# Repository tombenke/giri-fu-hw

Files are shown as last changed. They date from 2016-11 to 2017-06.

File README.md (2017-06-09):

giri-fu-hw v2.0
===============

Hardware module of the giri-fu functional unit, that is a simple relay board, with its own MCU.

It is a proof of concept for a tiny autonomous device, that is able to control 24 VAC magnetic valves in real circumstances:

- wet and dirty environment,
- wide range of temperature,
- mechanical stress.

The [functional block diagram of the unit](docs/images/giri-fu-hw_fbd.png) below demonstrates how to connect it into its environment:

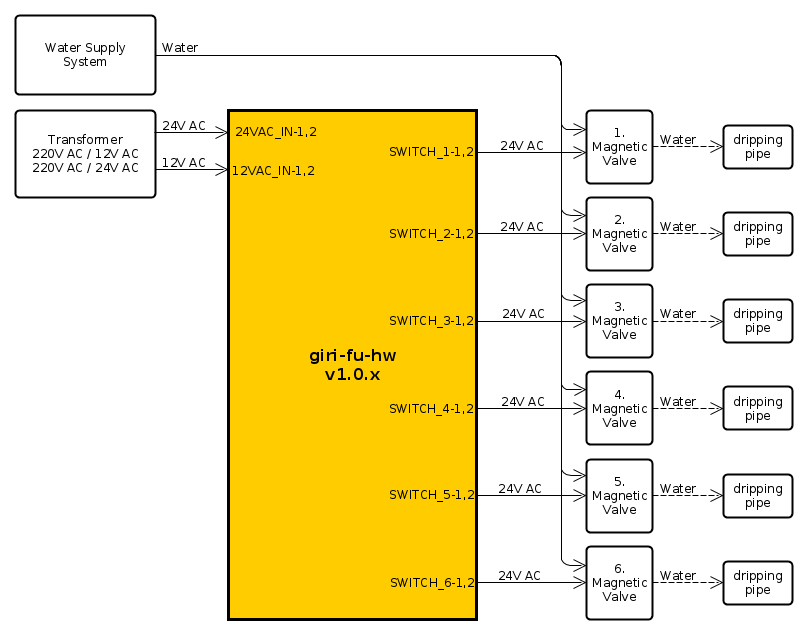
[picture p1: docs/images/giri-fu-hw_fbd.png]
functional block diagram of the unit


The v1.0.x version is just documenting [the early prototype](docs/images/prototype.jpg?raw=true "giri-fu-hw prototype"),
that was made on a raster panel. (Note: The PCB design differs from the raster panel version).

The PCB layout was intentionally designed to be very simple, in order to make it easy to reproduce with DIY technologies.

The top layer can be substituted with, straight jumper wires, so it is enought to make a one-sided panel, with the bottom layout.

The firmware implementation can be found in the [giri-fu firmware repository](https://github.com/tombenke/giri-fu).

## Features

- Standalone MCU (ATMega328P, 16MHz)
- High-voltage, high-current darlington transistor array (ULN2003A)
- 6 relays to switch 24V AC current, for magnetic valves (RSY-5)
- 12V AC input for Power supply
- RS-485 serial communication port

Dimensions: 3.6 x 2.15 x 0.5 inch

Boxing: The minimum required internal size of box: 4.75 x 3 x 1.5 inch

Mounting: N.A.

Inputs:

- 12V AC, min: ? A (TBD.)
- 24V AC, min: ? A (TBD.)

Outputs (6x):

- Carry current: 2 A
- Max. operating voltage: 125 VAC, 60 VDC
- Max. operating current: 1 A
- Max. switching capacity: 62.50 VA, 30W
- Min. permissible load: 1 mA, 5 VDC

## Artifacts

The `src` folder holds the EAGLE files:

- `src/giri-fu-hw.sch`
- `src/giri-fu-hw.brd`

The `dist` folder contains the final products for manufacturing:

- [The schematic diagram](dist/giri-fu-hw_sch.pdf)
- [The PCB layout](dist/giri-fu-hw_brd.pdf)
- [PCB top layer (to print)](dist/giri-fu-hw_top.pdf)
- [PCB bottom layer (to print)](dist/giri-fu-hw_bottom.pdf)

## References

- [giri-fu firmware](https://github.com/tombenke/giri-fu)
- [ATMega328P datasheet](http://www.atmel.com/Images/Atmel-42735-8-bit-AVR-Microcontroller-ATmega328-328P_datasheet.pdf)
- [Rayex RSY-5 relay datasheet](docs/datasheets/RSY-5G5V1K5V1_EN.pdf)
- [ULN2003A datsheet](https://www.sparkfun.com/datasheets/IC/ULN2003A.pdf)
- [Making of PCBs at home, DIY using inexpenive materials](https://www.youtube.com/watch?v=mv7Y0A9YeUc)
- [Heatless (cold) Toner Transfer (for PCB)](https://www.youtube.com/watch?v=HBIxvwZ_0og)
- [yEd - GraphML Editor, used for Functional Block Diagram creation](http://www.yworks.com/products/yed)
- [EAGLE PCB Design tool](https://cadsoft.io/)

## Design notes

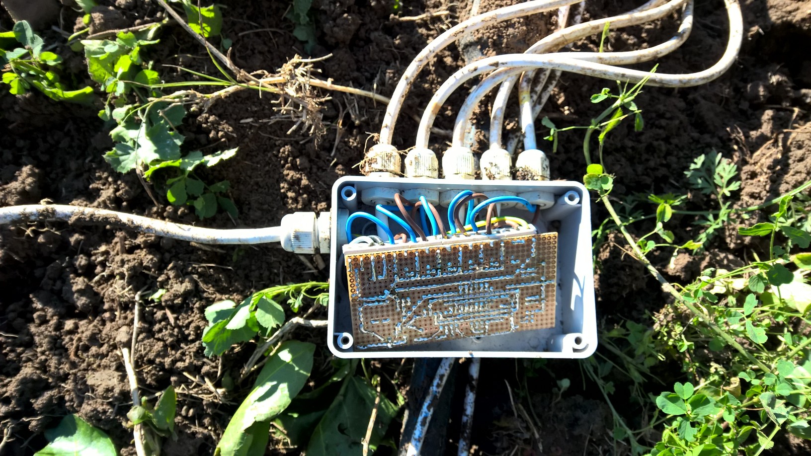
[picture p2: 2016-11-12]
docs/images/prototype.jpg

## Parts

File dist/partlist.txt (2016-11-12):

Partlist

Exported from giri-fu-hw.brd at 2016.11.12. 7:37

EAGLE Version 6.5.0 Copyright (c) 1988-2013 CadSoft

Assembly variant: 

Part     Value          Package      Library      Position (inch)       Orientation

C1       22p            C025-025X050 rcl          (1.75 1.65)           R0
C2       22p            C025-025X050 rcl          (1.5 1.65)            R0
C3       100n           C025-025X050 rcl          (1.85 1.4)            R270
C4       10uF           E2-5         adafruit     (2 1.4)               R270
C5                      E35-12       rcl          (0.95 1.35)           R180
D1       1N4004         DO41-10      diode        (0.7 0.5)             R0
D2       1N4004         DO41-10      diode        (0.5 0.65)            R0
D3       1N4004         DO41-10      diode        (0.5 0.95)            R180
D4       1N4004         DO41-10      diode        (0.7 0.8)             R180
IC1      ATMEGA168-20P  DIL28-3      adafruit     (2.65 1.85)           R180
IC2      7805T          TO220H       linear       (0.75 1.85)           R90
IC3      ULN2003AN      DIL16        uln-udn      (2.95 1.35)           R180
ISP1     AVRISP-6       AVRISP       adafruit     (2.4 1.35)            R0
K1       G5V1           G5V1         relay        (3.2 0.65)            R90
K2       G5V1           G5V1         relay        (2.8 0.65)            R90
K3       G5V1           G5V1         relay        (2.4 0.65)            R90
K4       G5V1           G5V1         relay        (2 0.65)              R90
K5       G5V1           G5V1         relay        (1.6 0.65)            R90
K6       G5V1           G5V1         relay        (1.2 0.65)            R90
Q1       16MHz          HC49U-V      adafruit     (1.6 1.85)            R180
R1       10K            0207/10      rcl          (2.15 1.4)            R270
R2       1M             0207/10      rcl          (1.6 2)               R180
X10                     W237-132     con-wago-508 (3.2 0.2)             R180
X11                     W237-132     con-wago-508 (2.8 0.2)             R180
X12                     W237-132     con-wago-508 (2.4 0.2)             R180
X13                     W237-132     con-wago-508 (2 0.2)               R180
X14                     W237-132     con-wago-508 (1.6 0.2)             R180
X15                     W237-132     con-wago-508 (1.2 0.2)             R180
X16                     W237-132     con-wago-508 (0.8 0.2)             R180
X17                     W237-132     con-wago-508 (0.4 0.2)             R180

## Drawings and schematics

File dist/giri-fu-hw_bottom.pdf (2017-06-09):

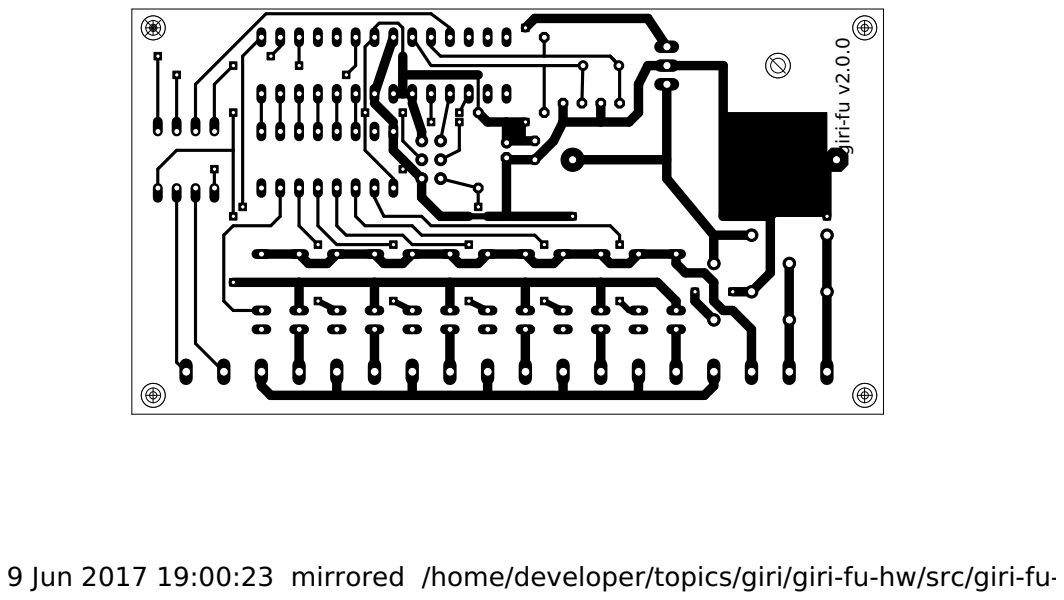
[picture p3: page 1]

9 Jun 2017 19:00:23 mirrored /home/developer/topics/giri/giri-fu-hw/src/giri-fu-hw.brd

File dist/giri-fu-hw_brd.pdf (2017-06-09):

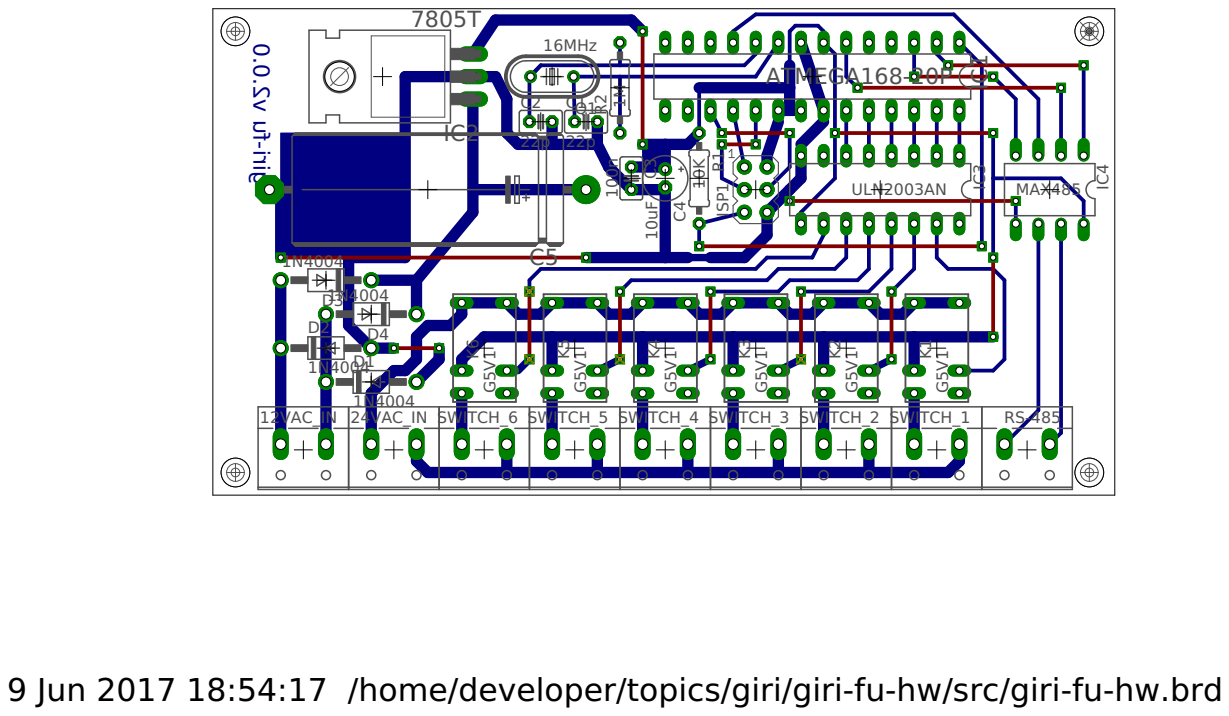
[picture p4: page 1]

9 Jun 2017 18:54:17 /home/developer/topics/giri/giri-fu-hw/src/giri-fu-hw.brd

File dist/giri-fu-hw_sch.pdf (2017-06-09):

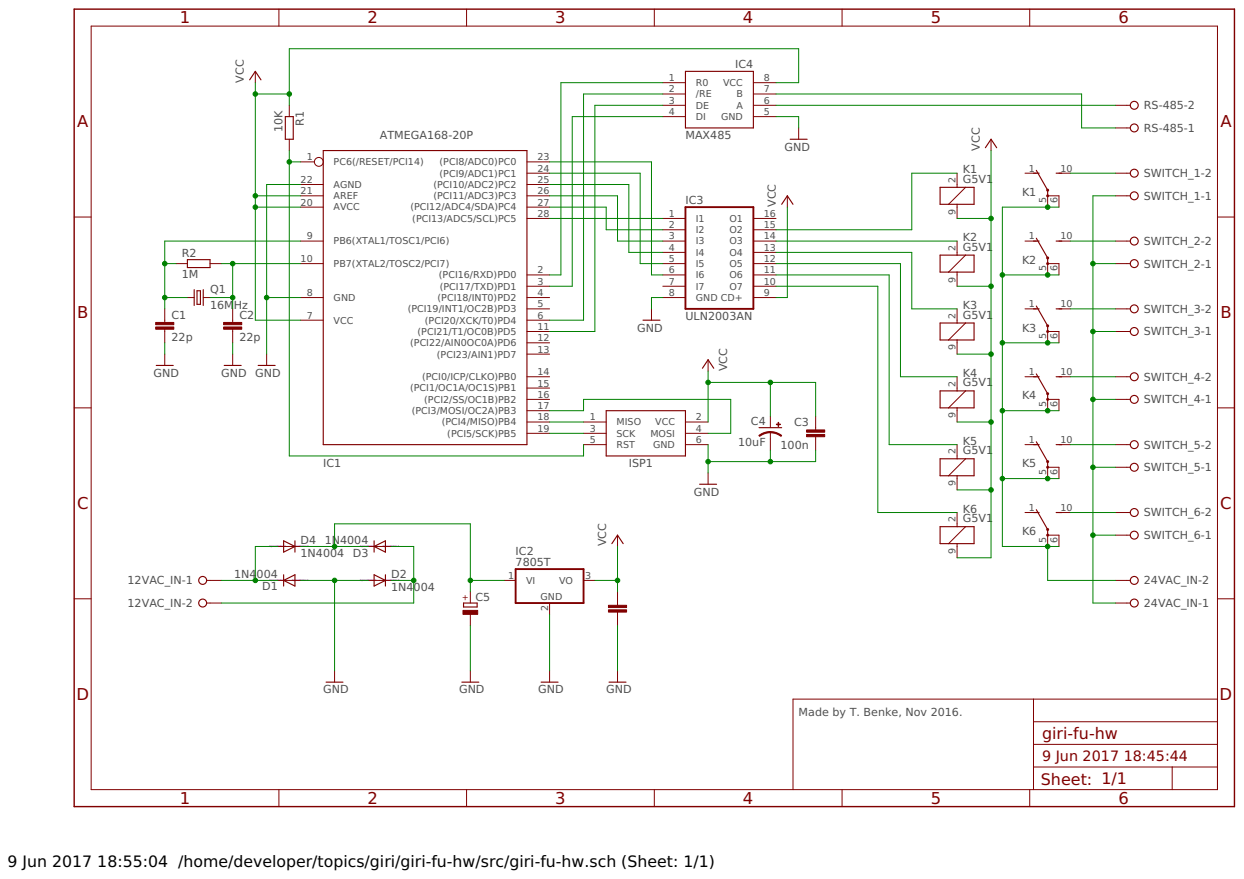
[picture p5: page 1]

24
25
26

5 | | 12
6 | | 11 O7

Made by T. Benke, Nov 2016.

Sheet: 1/1

9 Jun 2017 18:55:04 /home/developer/topics/giri/giri-fu-hw/src/giri-fu-hw.sch (Sheet: 1/1)

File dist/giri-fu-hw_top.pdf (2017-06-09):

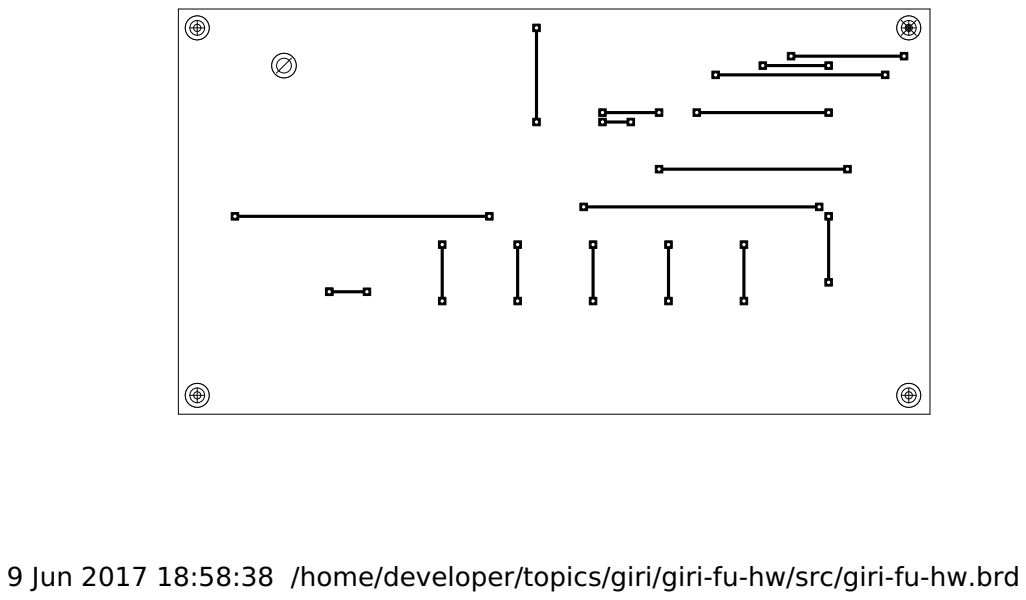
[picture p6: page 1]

9 Jun 2017 18:58:38 /home/developer/topics/giri/giri-fu-hw/src/giri-fu-hw.brd

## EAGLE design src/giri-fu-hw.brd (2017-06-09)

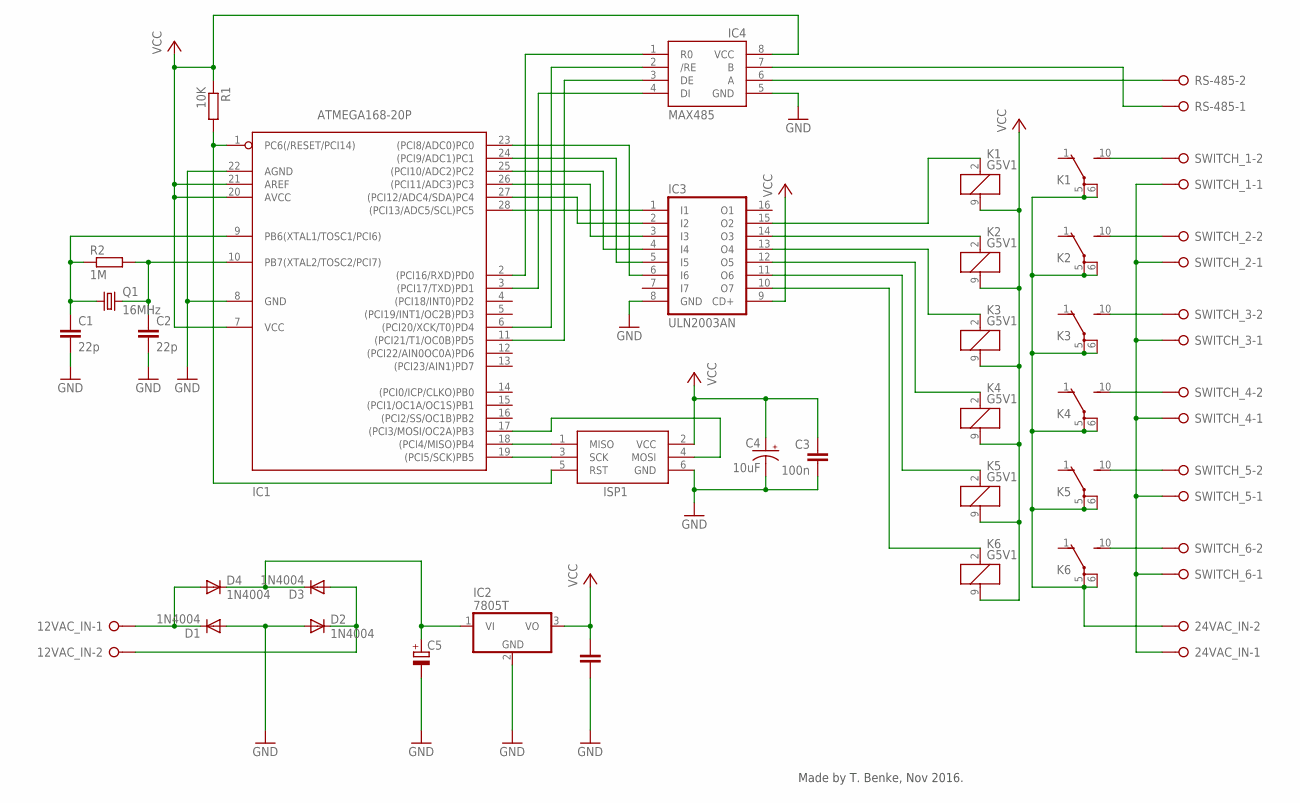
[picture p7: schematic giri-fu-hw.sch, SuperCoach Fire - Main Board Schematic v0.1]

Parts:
12VAC_IN, 24VAC_IN: W237-02P; W237-132
C1, C2: 22p; C025-025X050
C3: 100n; C025-025X050
C4: 10uF; E2-5
C5: CPOL-EUE35-12AXIAL; E35-12
D1, D2, D3, D4: 1N4004; DO41-10
IC1: ATMEGA168-20P; DIL28-3
IC2: 7805T; TO220H
IC3: ULN2003AN; DIL16
IC4: MAX485; DIL08
ISP1: AVRISP-6; AVRISP
K1, K2, K3, K4, K5, K6: G5V1
Q1: 16MHz; HC49U-V
R1: 10K; 0207/10
R2: 1M; 0207/10
RS-485: W237-02P; W237-132
SWITCH_1, SWITCH_2, SWITCH_3, SWITCH_4, SWITCH_5, SWITCH_6: W237-02P; W237-132

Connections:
GND: C1.2, C2.2, C3.2, C4.-, C5.-, D1.A, D2.A, IC1.8 (GND), IC1.22 (AGND), IC2.2 (GND), IC3.8 (GND), IC4.5 (GND), ISP1.6 (GND)
unnamed: IC1.23 ((PCI8/ADC0)PC0), IC3.6 (I6)
unnamed: IC1.24 ((PCI9/ADC1)PC1), IC3.5 (I5)
unnamed: 24VAC_IN.2, K1.5, K1.6, K2.5, K2.6, K3.5, K3.6, K4.5, K4.6, K5.5, K5.6, K6.5, K6.6
unnamed: IC1.25 ((PCI10/ADC2)PC2), IC3.4 (I4)
unnamed: IC1.28 ((PCI13/ADC5/SCL)PC5), IC3.1 (I1)
unnamed: IC1.26 ((PCI11/ADC3)PC3), IC3.3 (I3)
unnamed: IC1.27 ((PCI12/ADC4/SDA)PC4), IC3.2 (I2)
unnamed: C3.1, C4.+, IC1.7 (VCC), IC1.20 (AVCC), IC1.21 (AREF), IC2.3 (VO), IC3.9 (CD+), IC4.8 (VCC), ISP1.2 (VCC), K1.9 (2), K2.9 (2), K3.9 (2), K4.9 (2), K5.9 (2), K6.9 (2), R1.1
unnamed: IC3.10 (O7), K6.2 (1)
unnamed: IC3.11 (O6), K5.2 (1)
unnamed: IC1.19 ((PCI5/SCK)PB5), ISP1.3 (SCK)
unnamed: IC1.17 ((PCI3/MOSI/OC2A)PB3), ISP1.4 (MOSI)
unnamed: IC1.1 (PC6(/RESET/PCI14)), ISP1.5 (RST), R1.2
unnamed: C1.1, IC1.9 (PB6(XTAL1/TOSC1/PCI6)), Q1.1, R2.1
unnamed: C2.1, IC1.10 (PB7(XTAL2/TOSC2/PCI7)), Q1.2, R2.2
unnamed: IC1.18 ((PCI4/MISO)PB4), ISP1.1 (MISO)
unnamed: IC3.12 (O5), K4.2 (1)
unnamed: IC3.13 (O4), K3.2 (1)
unnamed: IC3.14 (O3), K2.2 (1)
unnamed: IC3.15 (O2), K1.2 (1)
unnamed: C5.+, D3.C, D4.C, IC2.1 (VI)
unnamed: 12VAC_IN.1, D1.C, D4.A
unnamed: 12VAC_IN.2, D2.C, D3.A
unnamed: IC4.6 (A), RS-485.2
unnamed: IC4.7 (B), RS-485.1
unnamed: IC1.2 ((PCI16/RXD)PD0), IC4.1 (R0)
unnamed: IC1.3 ((PCI17/TXD)PD1), IC4.4 (DI)
unnamed: K1.10 (S), SWITCH_1.2
unnamed: K2.10 (S), SWITCH_2.2
unnamed: K3.10 (S), SWITCH_3.2
unnamed: K4.10 (S), SWITCH_4.2
unnamed: K5.10 (S), SWITCH_5.2
unnamed: K6.10 (S), SWITCH_6.2
unnamed: 24VAC_IN.1, SWITCH_1.1, SWITCH_2.1, SWITCH_3.1, SWITCH_4.1, SWITCH_5.1, SWITCH_6.1
unnamed: IC1.6 ((PCI20/XCK/T0)PD4), IC4.2 (/RE)
unnamed: IC1.11 ((PCI21/T1/OC0B)PD5), IC4.3 (DE)

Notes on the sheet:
Made by T. Benke, Nov 2016.

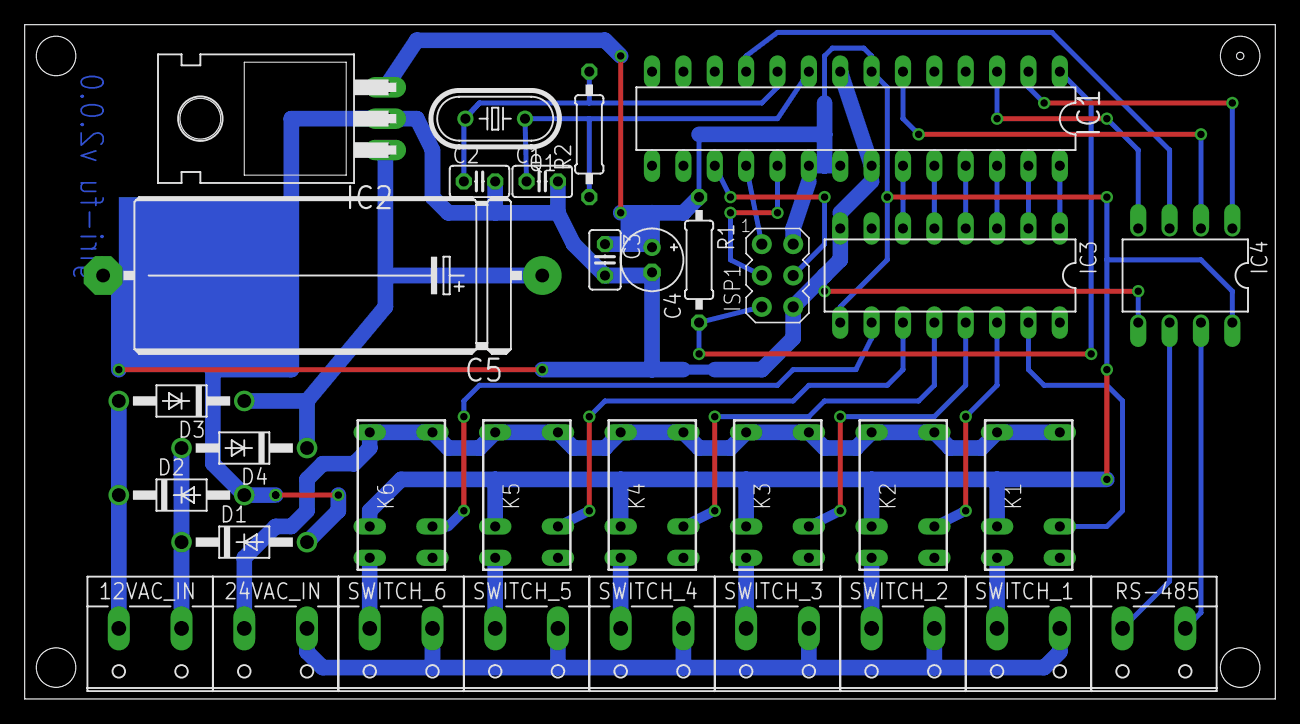
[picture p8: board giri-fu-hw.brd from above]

Board: 2 copper layers, 101.3 x 54.6 mm, 32 parts (0 on the bottom side), 37 nets.

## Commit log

2016-11-07 Initial import
    [giri-fu-hw.sch]
2016-11-12 Add Schematics Add PCB board design Add top and bottom prints for manual PCB manufacturing Add partlist Add photo on the prototype board Add datasheet to the RYS-5 relay
    [giri-fu-hw.brd, giri-fu-hw.sch]
2016-11-12 Rename prototype image Write README content
2016-11-12 Add extension to prototype link
2016-11-12 fix typo in .gitignore rename and replace schema and board files in README Add a new board pdf
    [giri-fu-hw.brd]
2016-11-12 Rename inputs and outputs Regenerate dist artifacts
    [giri-fu-hw.brd, giri-fu-hw.sch]
2016-11-24 Add link about PCB making to README
2017-03-15 Change the relay driver endpoint from ground to vcc
    [giri-fu-hw.brd, giri-fu-hw.sch]
2017-06-09 Add RS485 adapter
    [giri-fu-hw.brd, giri-fu-hw.sch]
